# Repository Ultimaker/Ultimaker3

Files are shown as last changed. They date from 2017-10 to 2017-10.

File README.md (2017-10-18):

# Ultimaker 3
Ultimaker 3 Hardware Files

In this repository, you will find the documentation and hardware designs for all parts of the Ultimaker 3. The bill of materials (BOM) directory lists all parts, with part numbers, quantities and raw materials. Print core AA and print core BB have a separate BOM.

The electronics files can be found in the PCB files directory.
If you are missing a part or information feel free to file an issue on GitHub.

Harma Woldhuis <br>
Ultimaker

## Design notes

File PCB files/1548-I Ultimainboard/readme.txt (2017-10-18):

The UltiMainboard 2.x.x electronics are released under GPLv2 license.
And are based on the original Ultimaker electronics design by Jan-Jaap Schuurman, Siert Wijnia and ErikDeBruijn at http://reprap.org/wiki/Ultimaker's_v1.5.7_PCB
As well as the ArduinoMega2560 by Arduino: http://arduino.cc/en/Main/arduinoBoardMega2560

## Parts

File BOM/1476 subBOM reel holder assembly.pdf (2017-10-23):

1476 Reel holder assembly

Total quantity parts | | 7
Part number | | Name | Quantity | material
1724 | F | NFC spool holder | 1 | PC-ABS
1725 | G | NFC PCB cover | 1 | PC-ABS
1726 | B | NFC PCB Antenna | 1 | Multiple
1727 | C | NFC PCB Cable | 1 | Multiple
1728 | C | NFC PCB Cable Cover | 1 | 1.4301 (X5CrNi18-10)
1729 | H | Filament Guide Frame | 1 | PC-ABS
1734 | F | Filament Guide | 1 | POM Acetal Copolymer

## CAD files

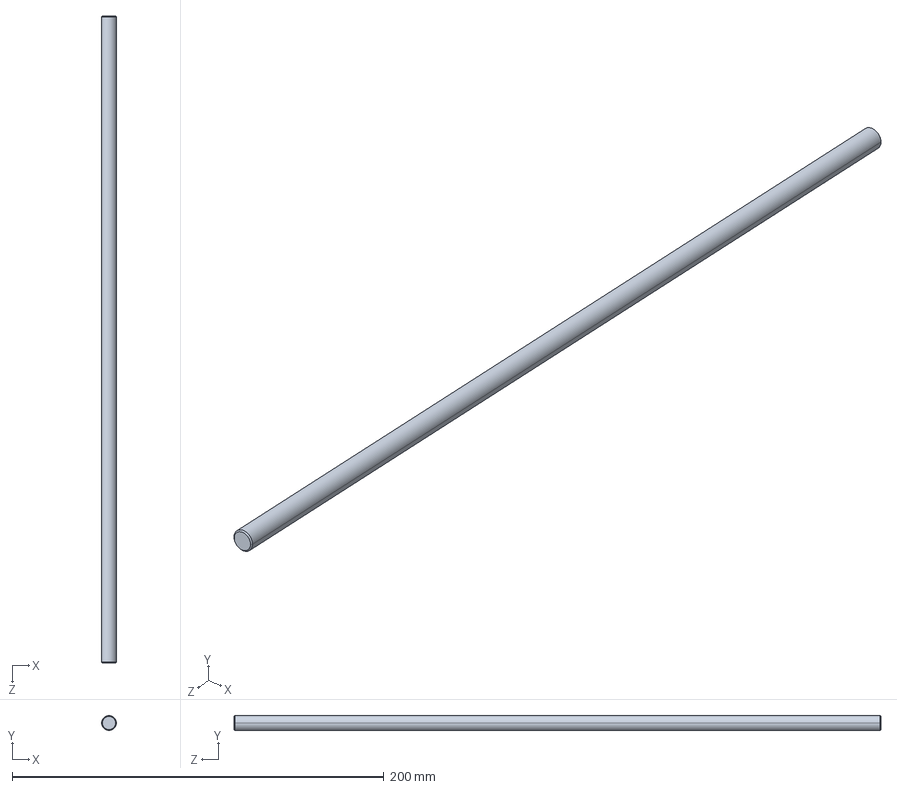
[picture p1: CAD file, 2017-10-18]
1011/1011-E/1011-E.STEP
8.00 x 8.00 x 348.0 mm

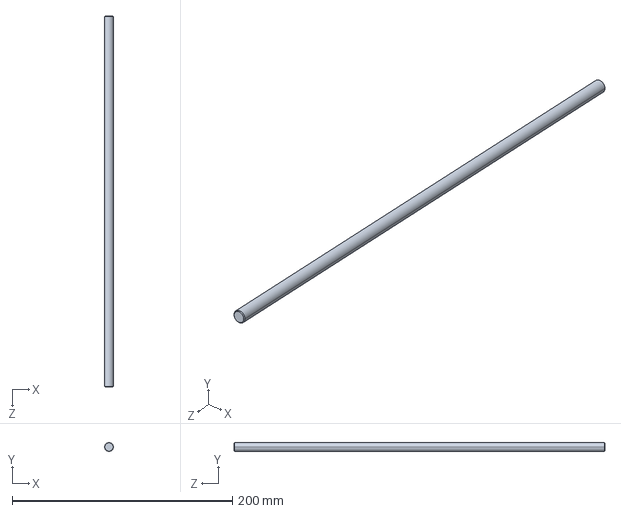
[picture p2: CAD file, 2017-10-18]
1012/1012-E/1012-E.STEP
8.00 x 8.00 x 337.0 mm

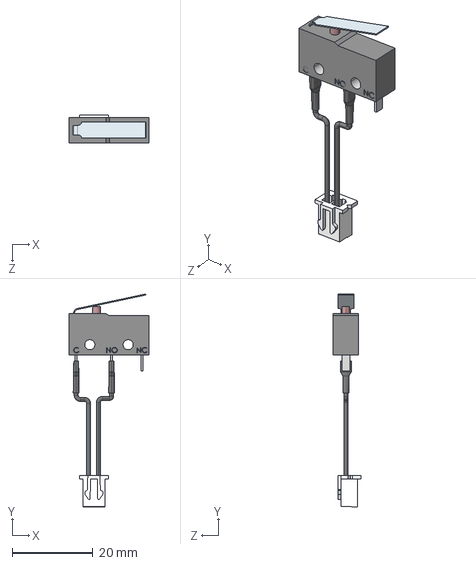
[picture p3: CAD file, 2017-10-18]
1024/1024-F/1024-F.STEP
19.8 x 52.9 x 6.90 mm

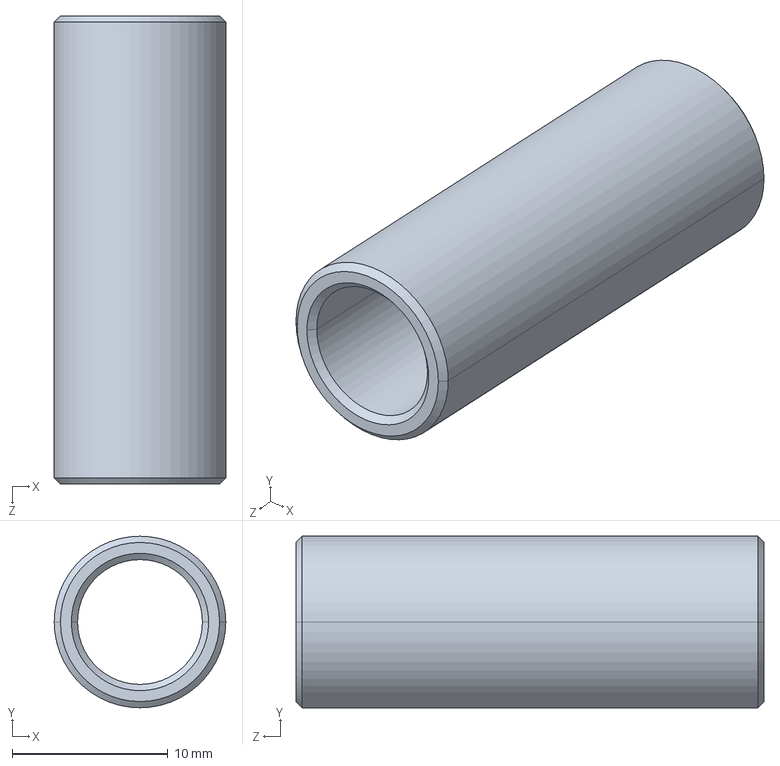
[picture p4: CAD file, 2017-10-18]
1056/1056-B/1056-B.STEP
11.0 x 11.0 x 30.0 mm

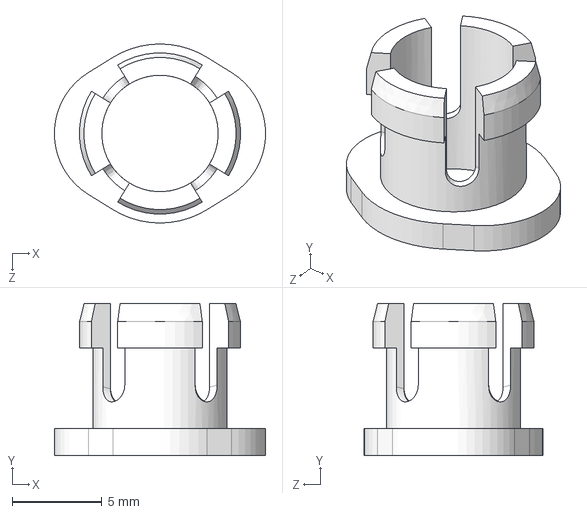
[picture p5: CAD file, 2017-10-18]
1069/1069-C/1069-C.STEP
11.8 x 8.50 x 10.00 mm

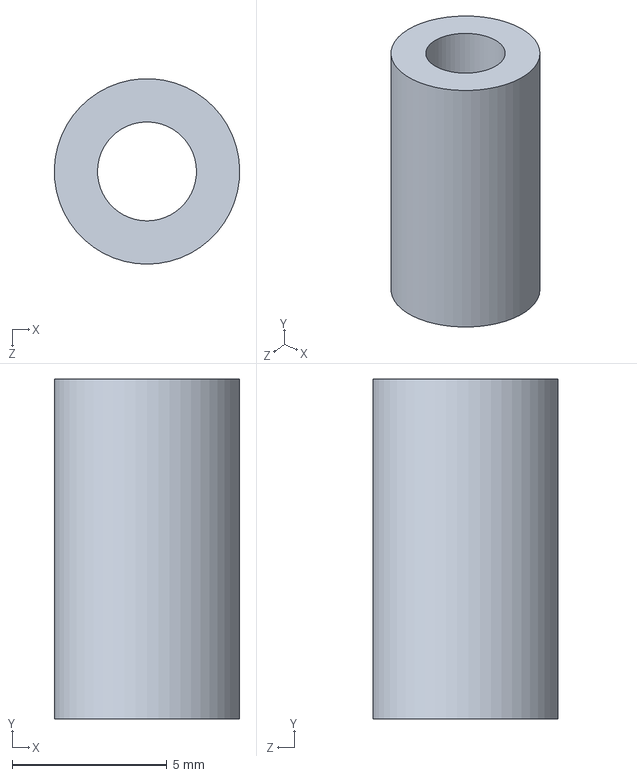
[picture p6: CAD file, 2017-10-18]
1083/1083-A/1083-Z1P-A.STEP
6.00 x 11.0 x 5.99 mm

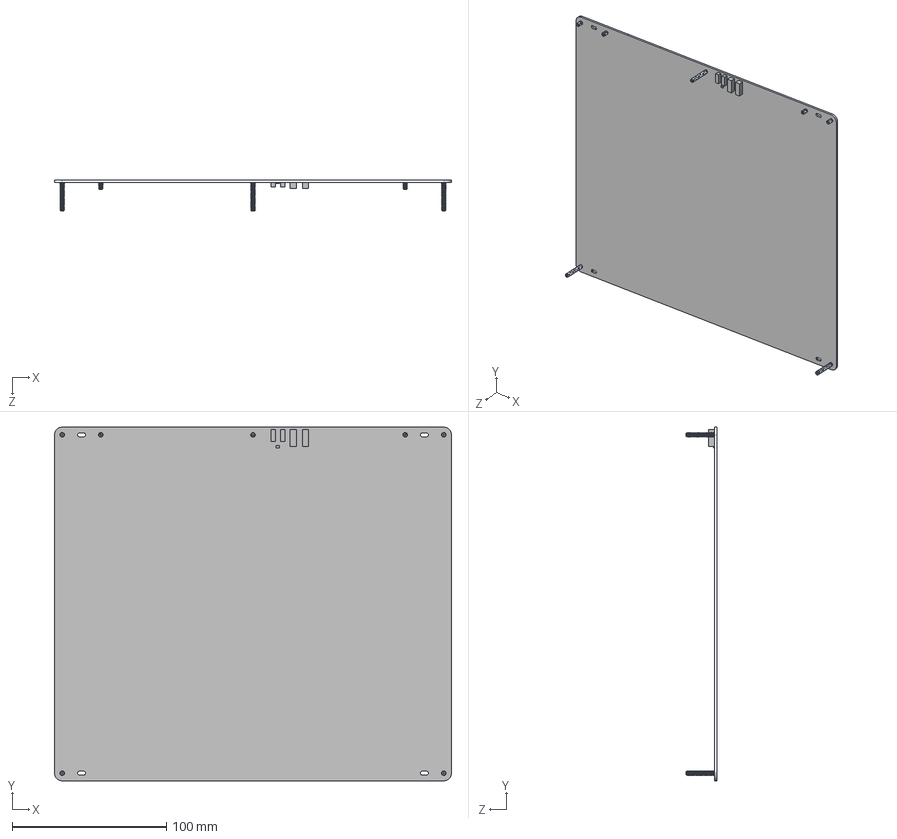
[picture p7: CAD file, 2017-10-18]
1155/1155-G/1155-G.STEP
257.0 x 229.0 x 20.0 mm
1155-D
FH-M3-xZI_FH-M3-6ZI x 4
FH-M3-xZI_FH-M3-20ZI x 3

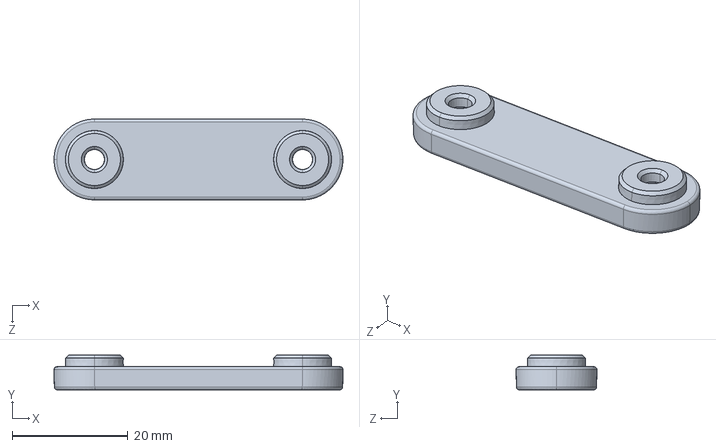
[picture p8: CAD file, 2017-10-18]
1156/1156-B/1156-B.STEP
50.0 x 6.00 x 14.0 mm

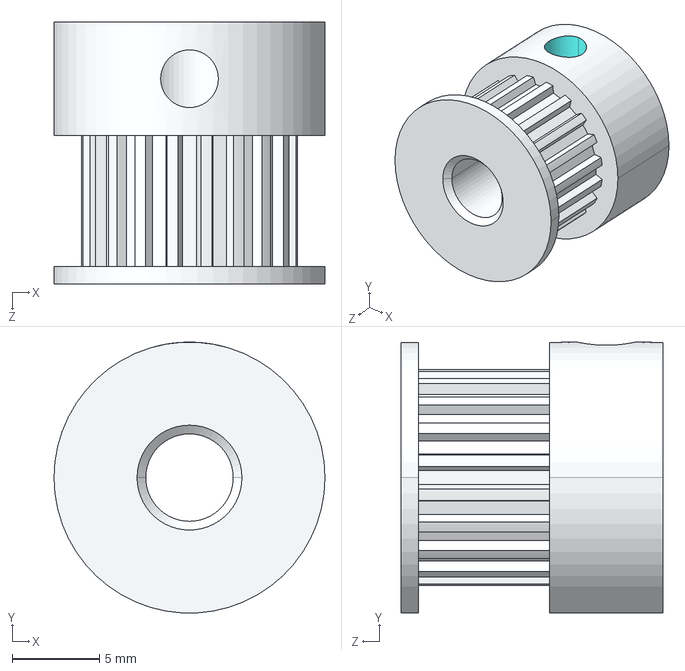
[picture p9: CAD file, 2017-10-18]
1165/1165-B/1165-B.STEP
15.5 x 15.5 x 15.0 mm

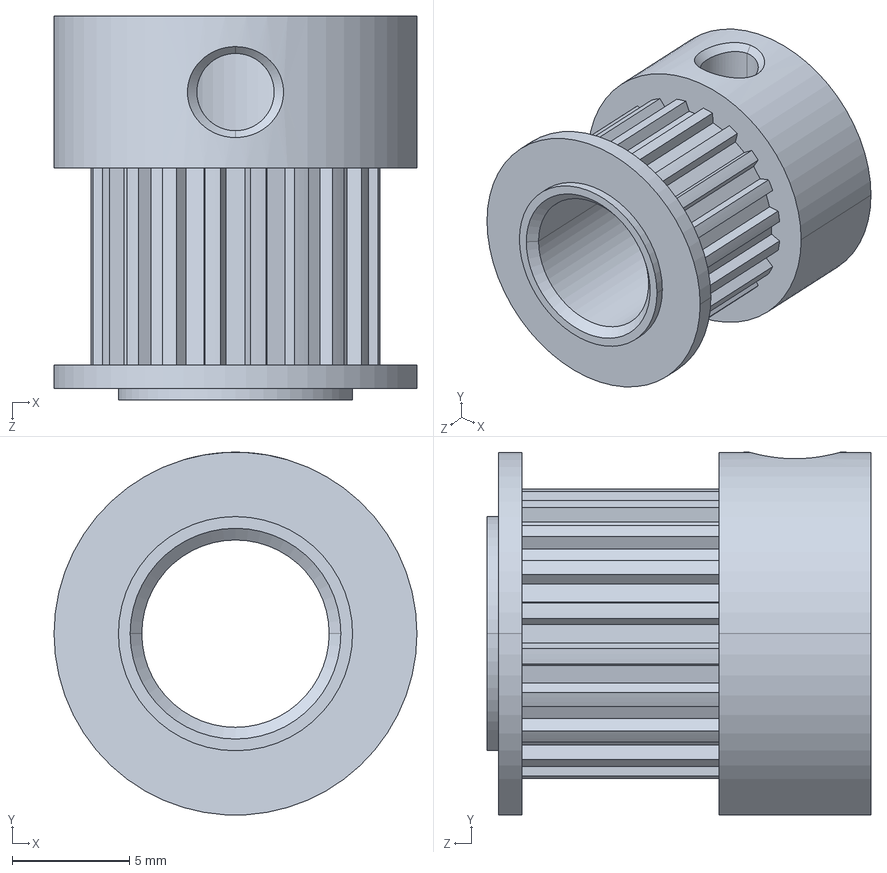
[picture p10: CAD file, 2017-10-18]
1166/1166-C/1166-C.STEP
15.5 x 15.5 x 16.4 mm

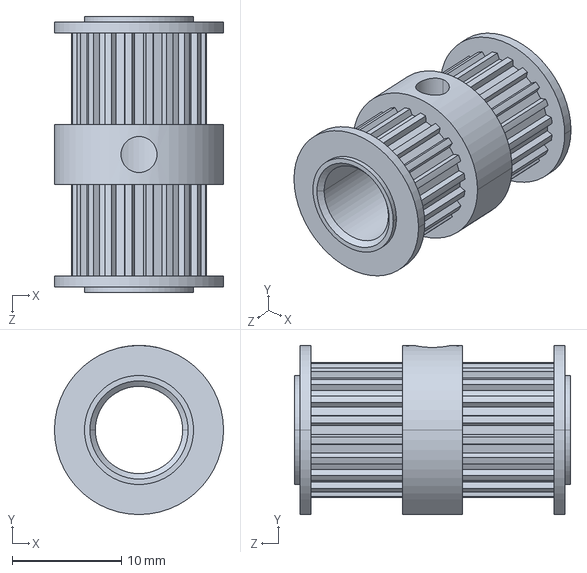
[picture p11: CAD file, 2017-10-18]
1167/1167-E/1167-E.STEP
15.5 x 15.5 x 25.3 mm

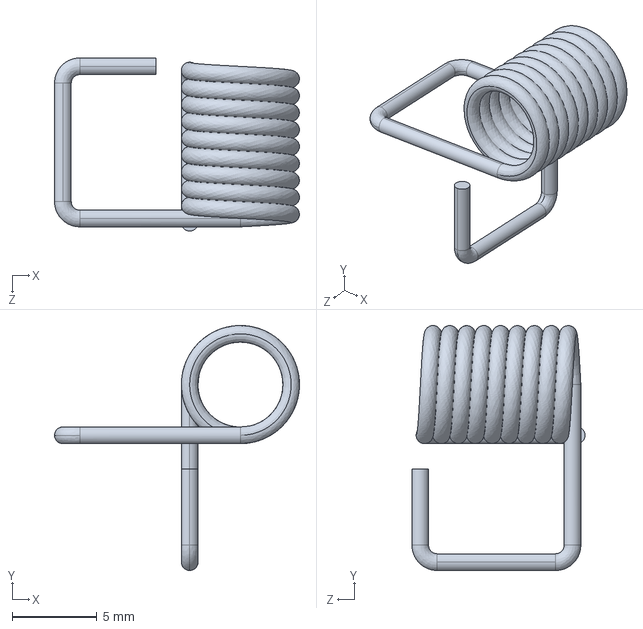
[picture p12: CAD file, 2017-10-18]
1168/1168-C/1168-C.STEP
14.5 x 14.5 x 10.2 mm

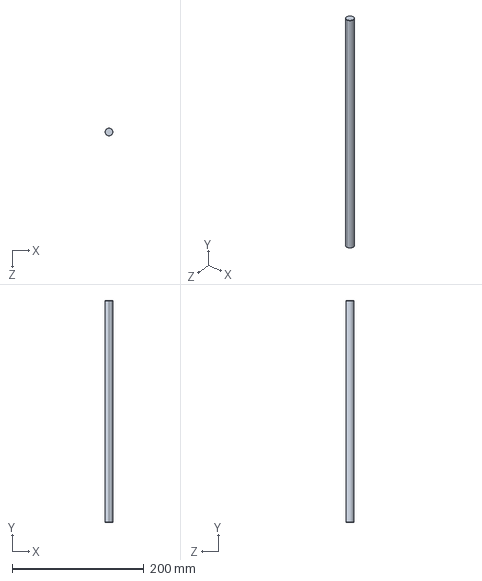
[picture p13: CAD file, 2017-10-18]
1169/1169-F/1169-F.STEP
12.0 x 337.0 x 12.0 mm

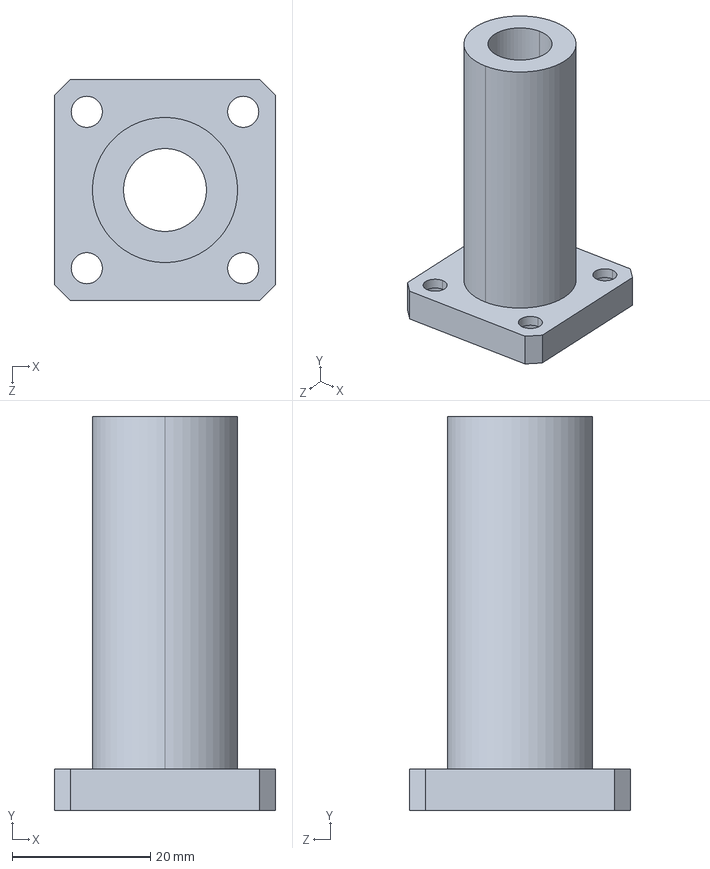
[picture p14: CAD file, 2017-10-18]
1170/1170-C/1170-C.STEP
32.0 x 57.0 x 32.0 mm

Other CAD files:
1172/1172-B/1172-B.STEP
1174/1174-A/1174-A.STEP
1175/1175-A/1175-A.STEP
1178/1178-B/1178-B.STEP
1187/1187-B/1187-B.STEP
1188/1188-A/1188-B2P-A.STEP
1200/1200-B/1200-B.STEP
1201/1201-D/1201-D.STEP
1202/1202-C/1202-C.STEP
1203/1203-C/1203-C.STEP
1204/1204-C/1204-C.STEP
1205/1205-C/1205-C.STEP
1206/1206-C/1206-C.STEP
1207/1207-C/1207-C.STEP
1209/1209-D/1209-D.STEP
1213/1213-C/1213-C.STEP
1214/1214-B/1214-B.STEP
1217/1217-B/1217-B.STEP
1220/1220-B/1220-B.STEP
1241/1241-C/1241-C.STEP
1244/1244-B/1244-B.STEP
1245/1245-D/1245-D.STEP
1252/1252-D/1252-D.STEP
1255/1255-B/1255-B.STEP
1256/1256-B/1256-B.STEP
1266/1266-D/1266-D.STEP
1279/1279-D/1279-D.STEP
1287/1287-B/1287-B.STEP
1288/1288-B/1288-B.STEP
1292/1292-A/1292-A.STEP
1294/1294-B/1294-B.STEP
1315/1315-B/1315-B.STEP
1354/1354-B/1354-B.STEP
1363/1363-D/1363-D.STEP
1479/1479-B/1479-B.STEP
1480/1480-B/1480-B.STEP
1481/1481-B/1481-B.STEP
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

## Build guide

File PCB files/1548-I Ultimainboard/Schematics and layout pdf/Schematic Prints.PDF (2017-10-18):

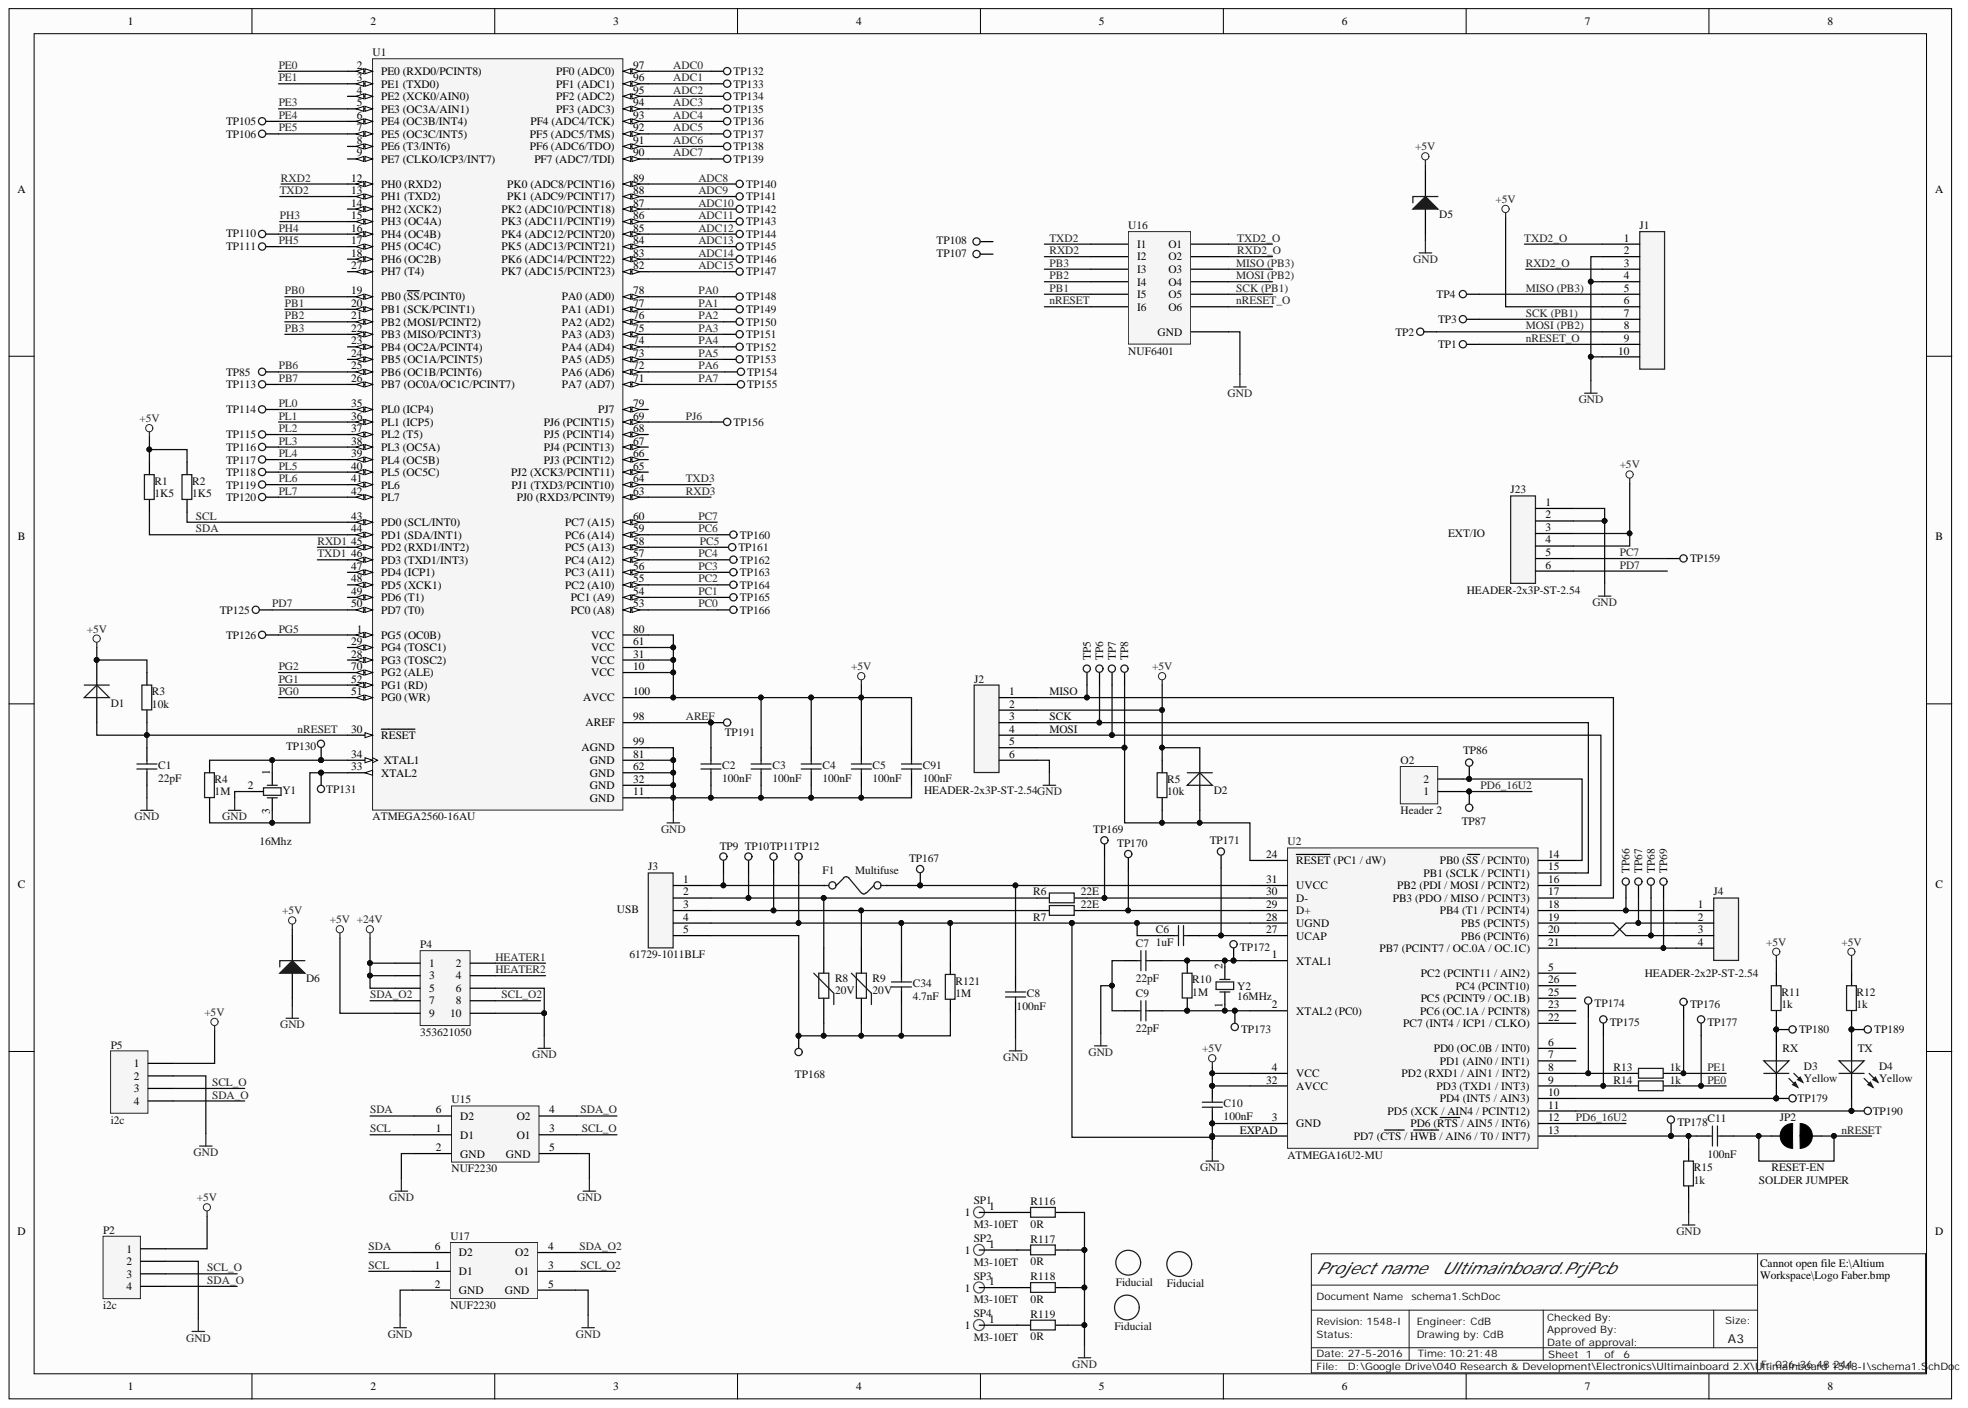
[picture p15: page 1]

3 | SCK
4 | MOSI

Project name Ultimainboard.PrjPcb

Cannot open file E:\Altium
Workspace\Logo Faber.bmp

Revision: 1548-I Status: | Engineer: CdB Drawing by: | Checked By: Approved By: Date of approval: | Size: A3

Date: 27-5-2016 | Time: 10:21:48 | Sheet of 6

D:\Google Drive\040 Research & Development\Electronics\Ultimainboard 2.X\Ultimainboard 1548-I\schema1.SchDoc

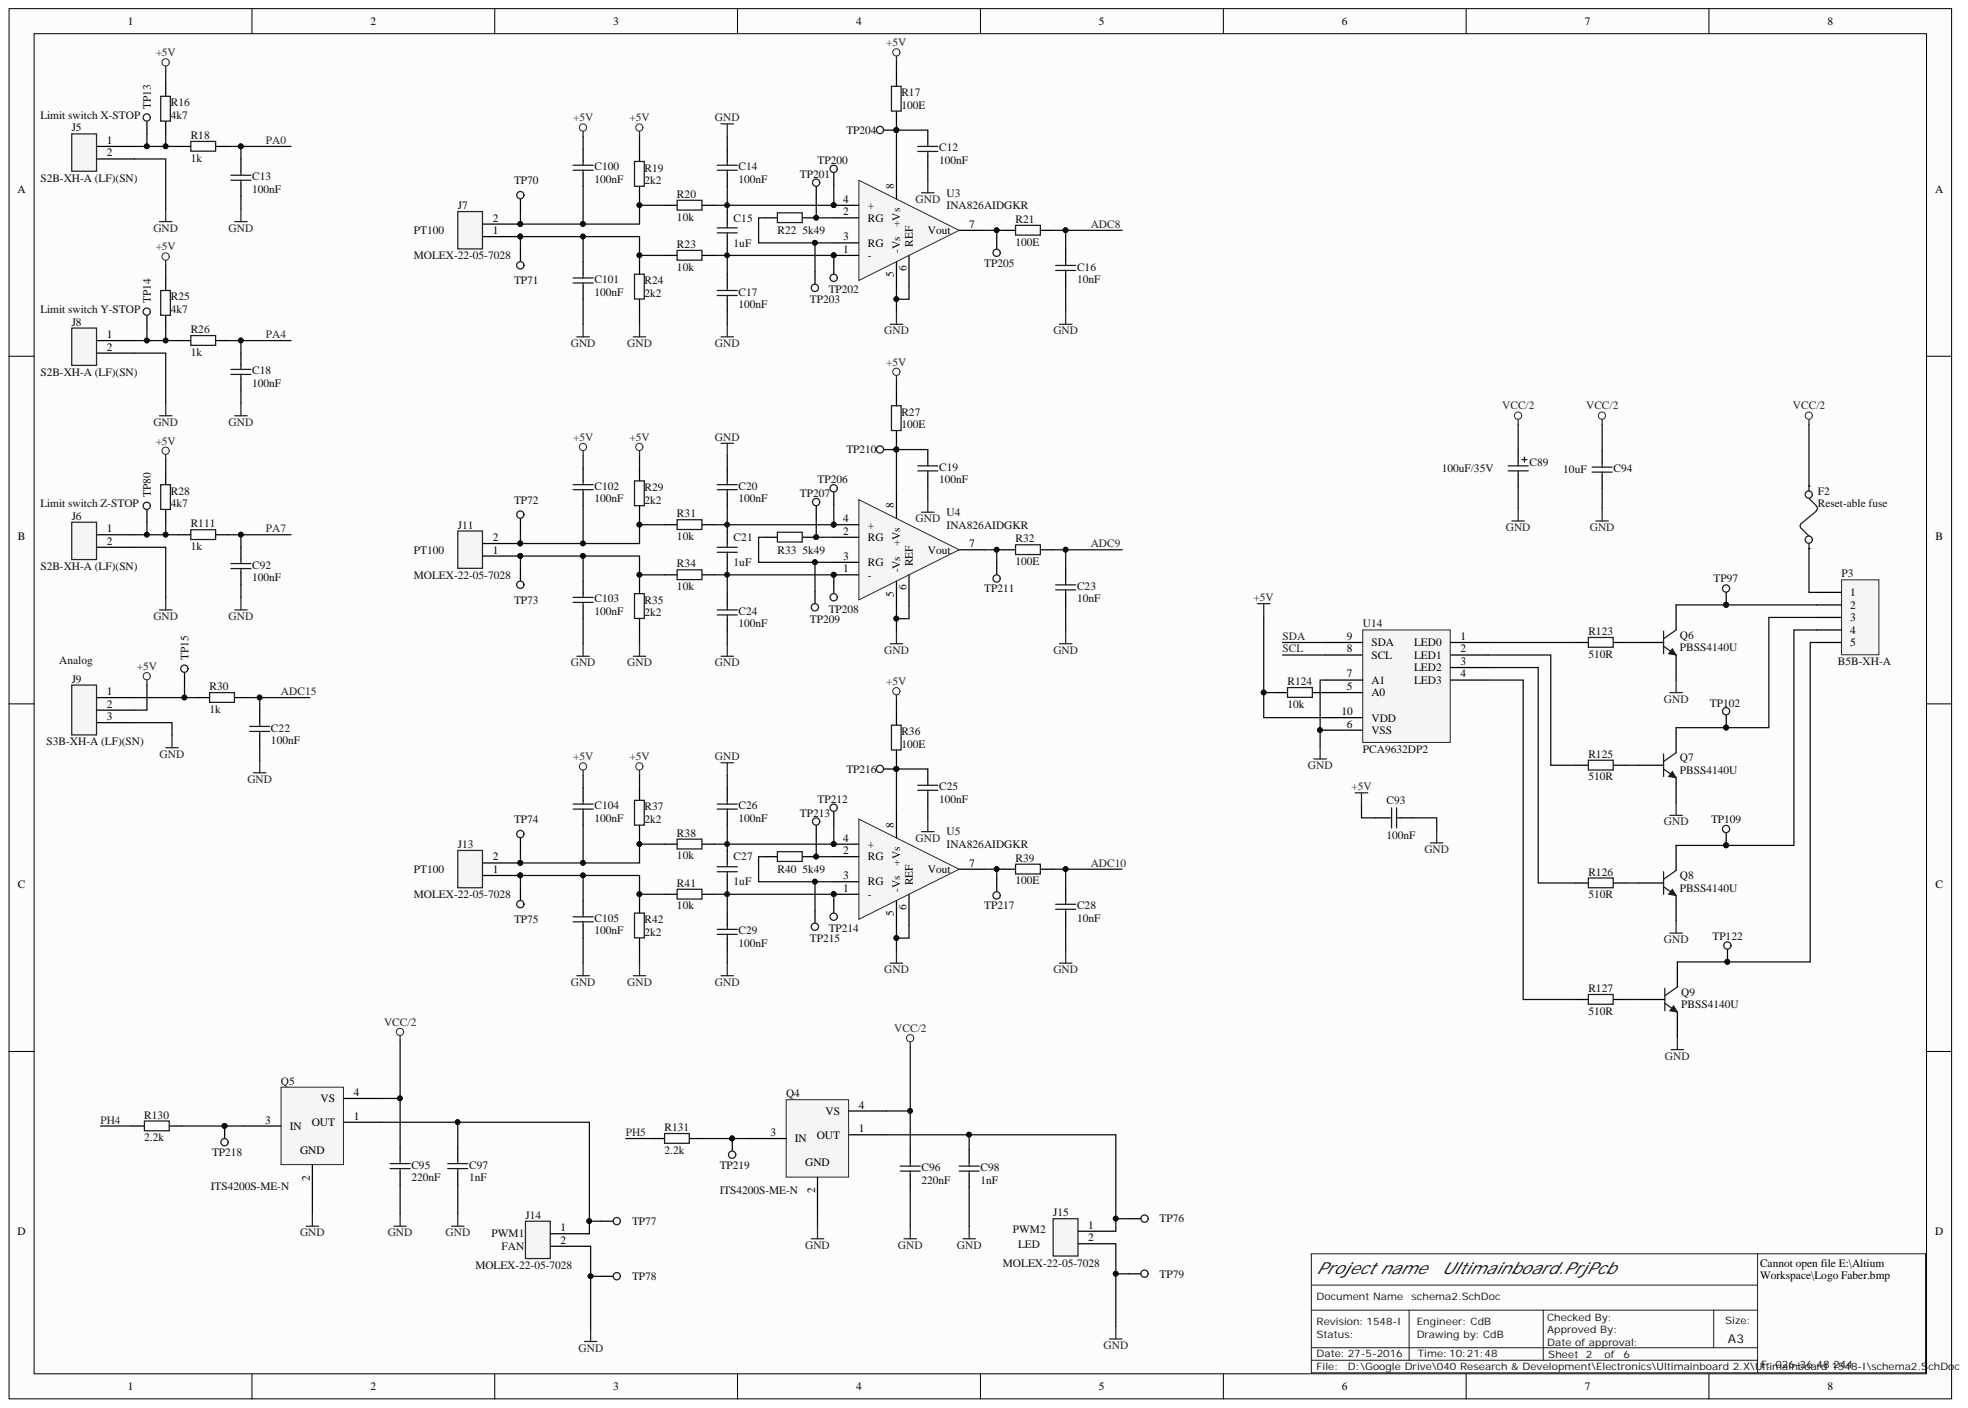
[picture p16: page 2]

Limit switch X-STOP Limit switch Y-STOP

Project name Ultimainboard.PrjPcb

Cannot open file E:\Altium
Workspace\Logo Faber.bmp

Engine e r : Cd B Dr a wing by: Cd B | Checke d By: A p p rove d By: Date of a p p roval: | Size : A

Date : 27-5-2016 | Time : 10:21:48 | She e t of

rch & Development\Electronics\Ultimainboa

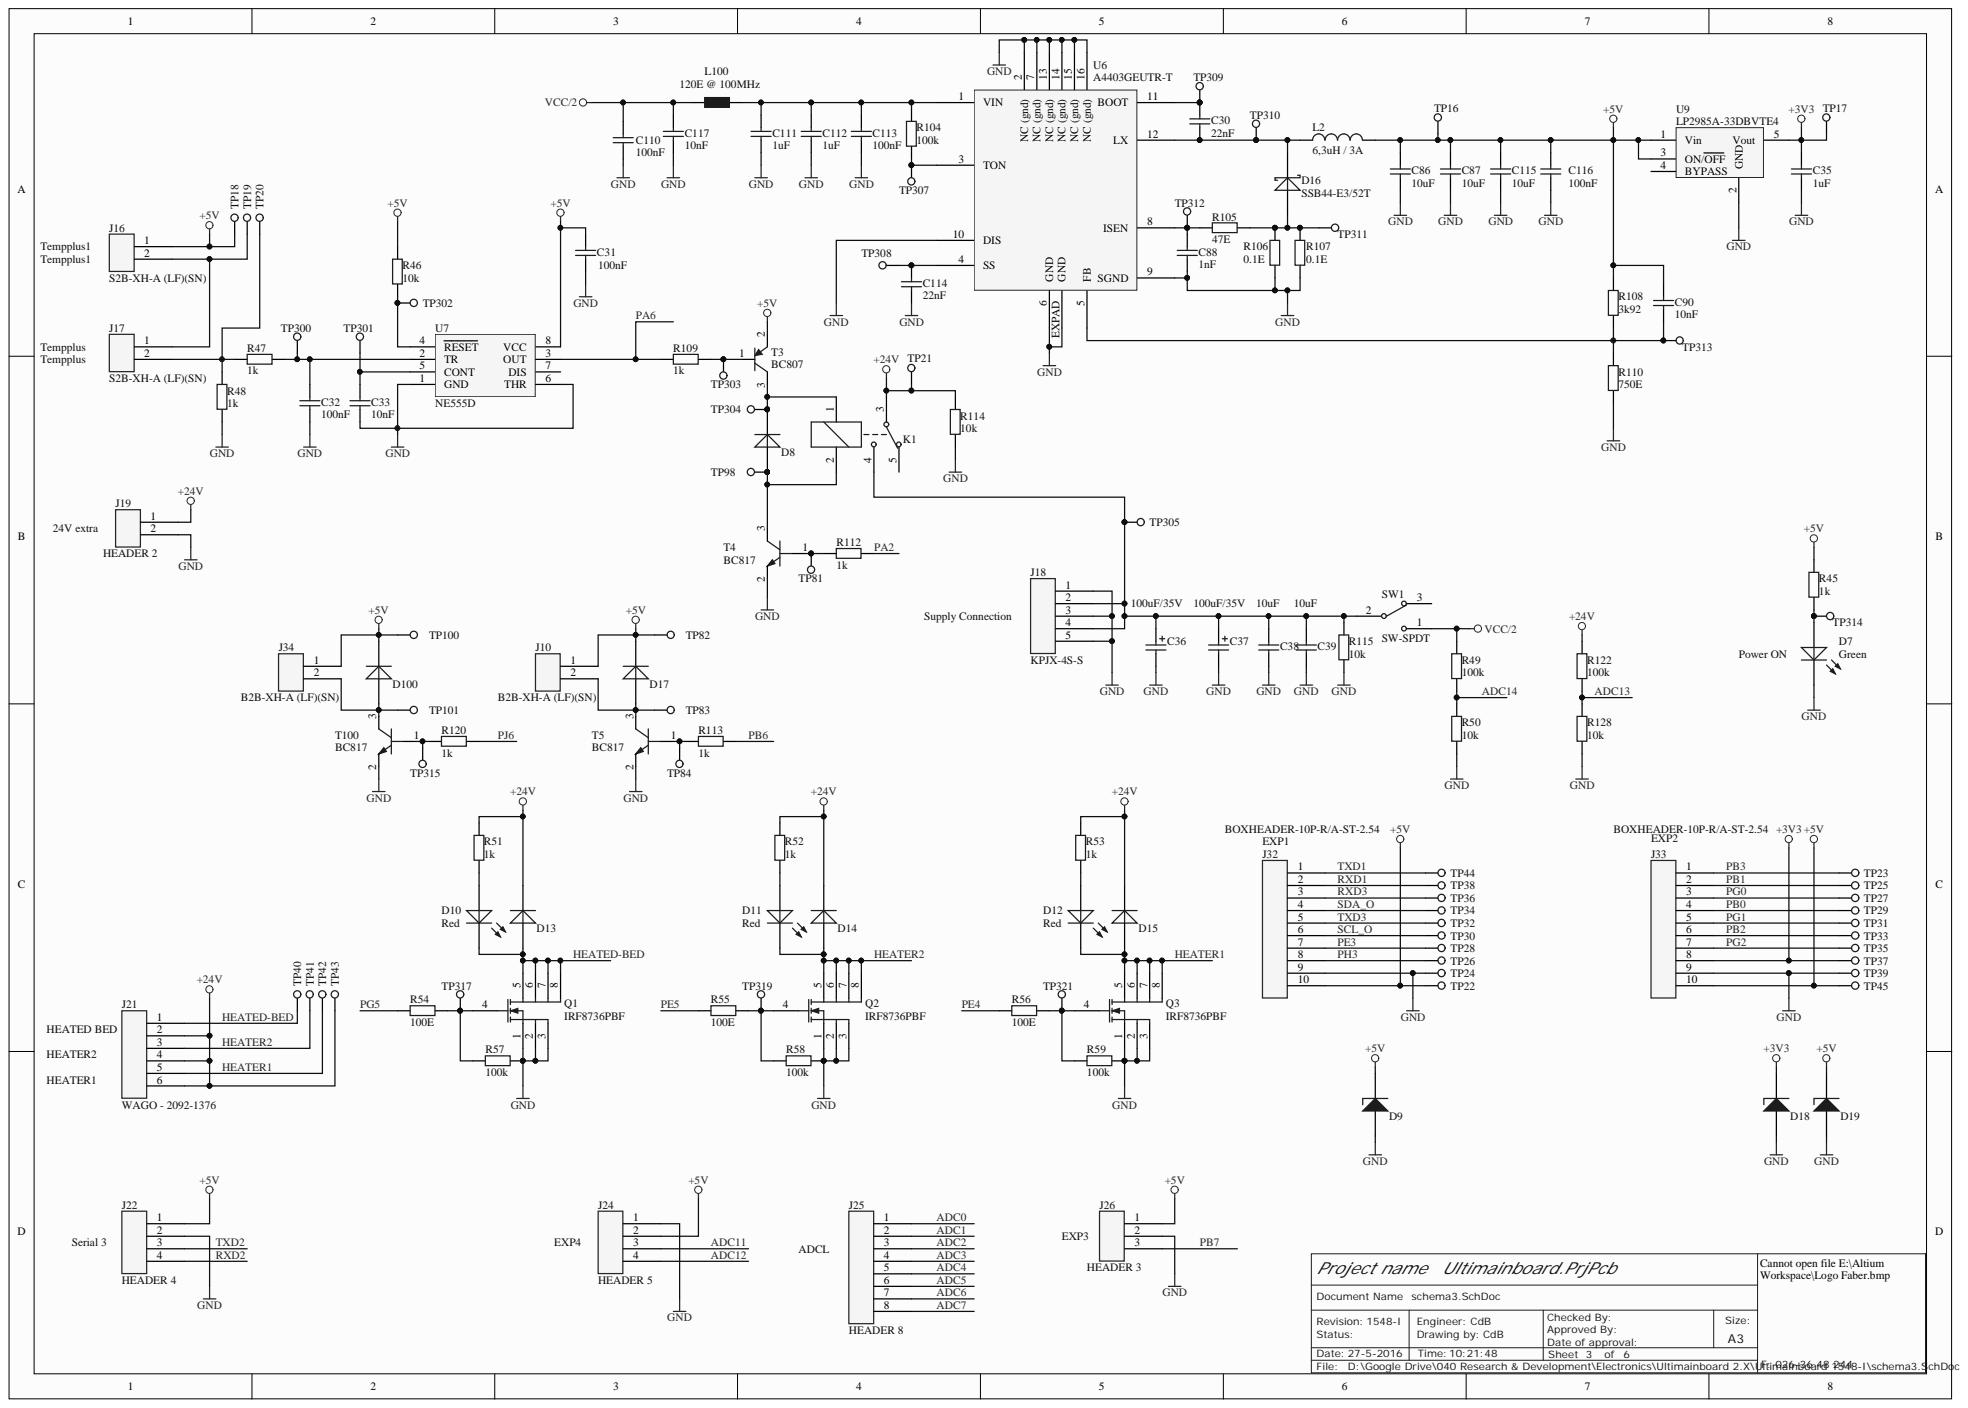
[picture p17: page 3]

TON 3

2 | HEATER2
4 | HEATER1

Project name Ultimainboard.PrjPcb

Cannot open file E:\Altium
Workspace\Logo Faber.bmp

D:\Google Drive\040 Research & Development\Electronics\Ultimainboard 2.X\Ultimainboard 1548-I\schema3.SchDoc

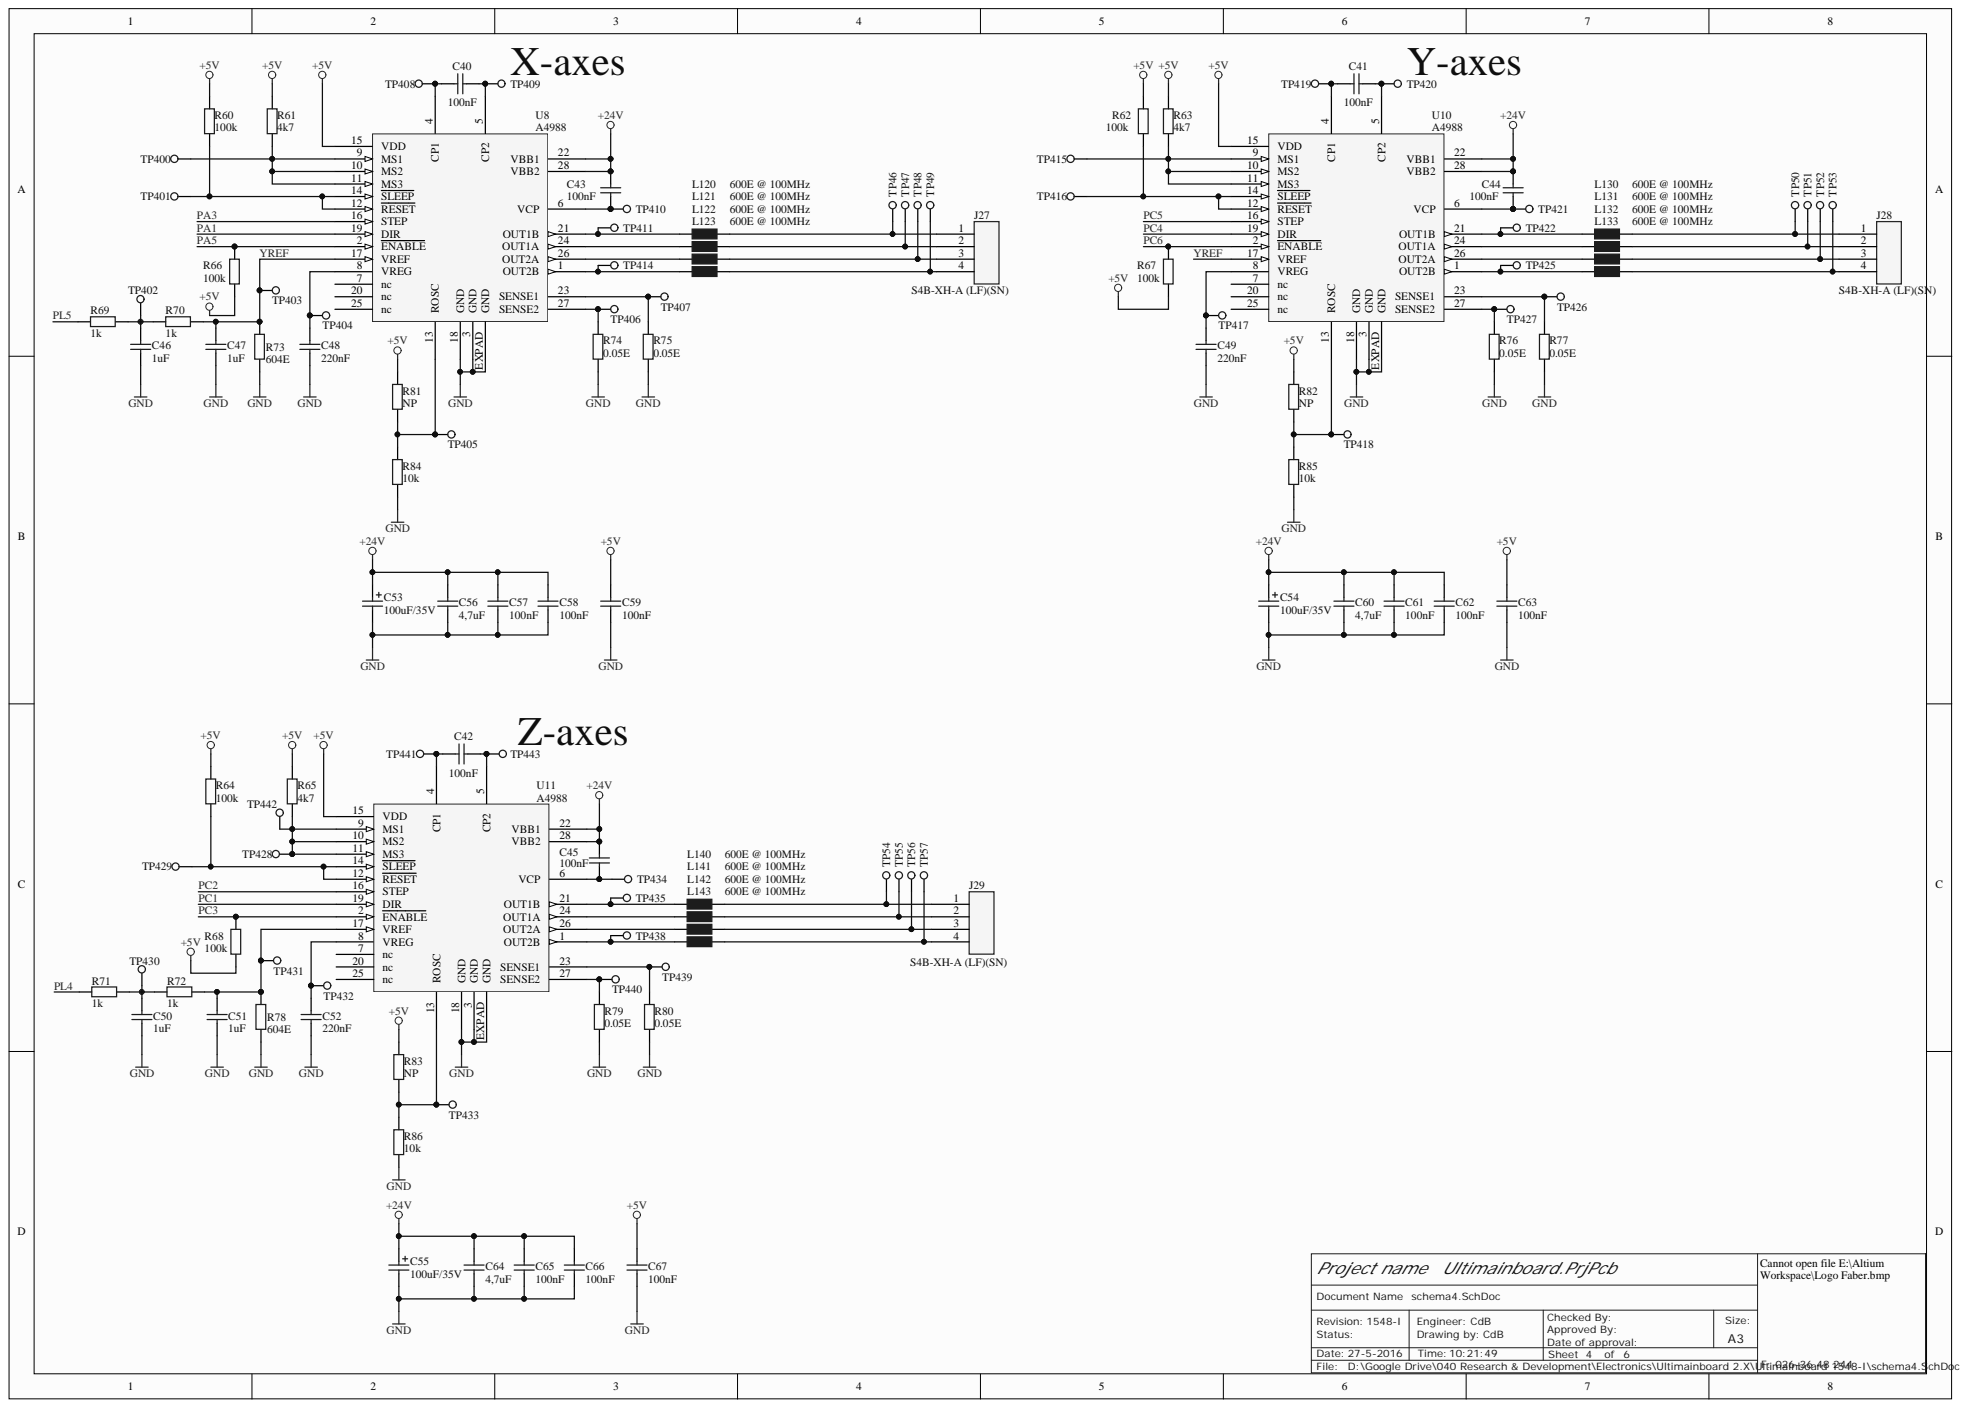
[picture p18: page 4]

VREG 8 | TP438 | 4
nc 7

Project name Ultimainboard.PrjPcb

Cannot open file E:\Altium
Workspace\Logo Faber.bmp

D:\Google Drive\040 Research & Development\Electronics\Ultimainboard 2.X\Ultimainboard 1548-I\schema4.SchDoc

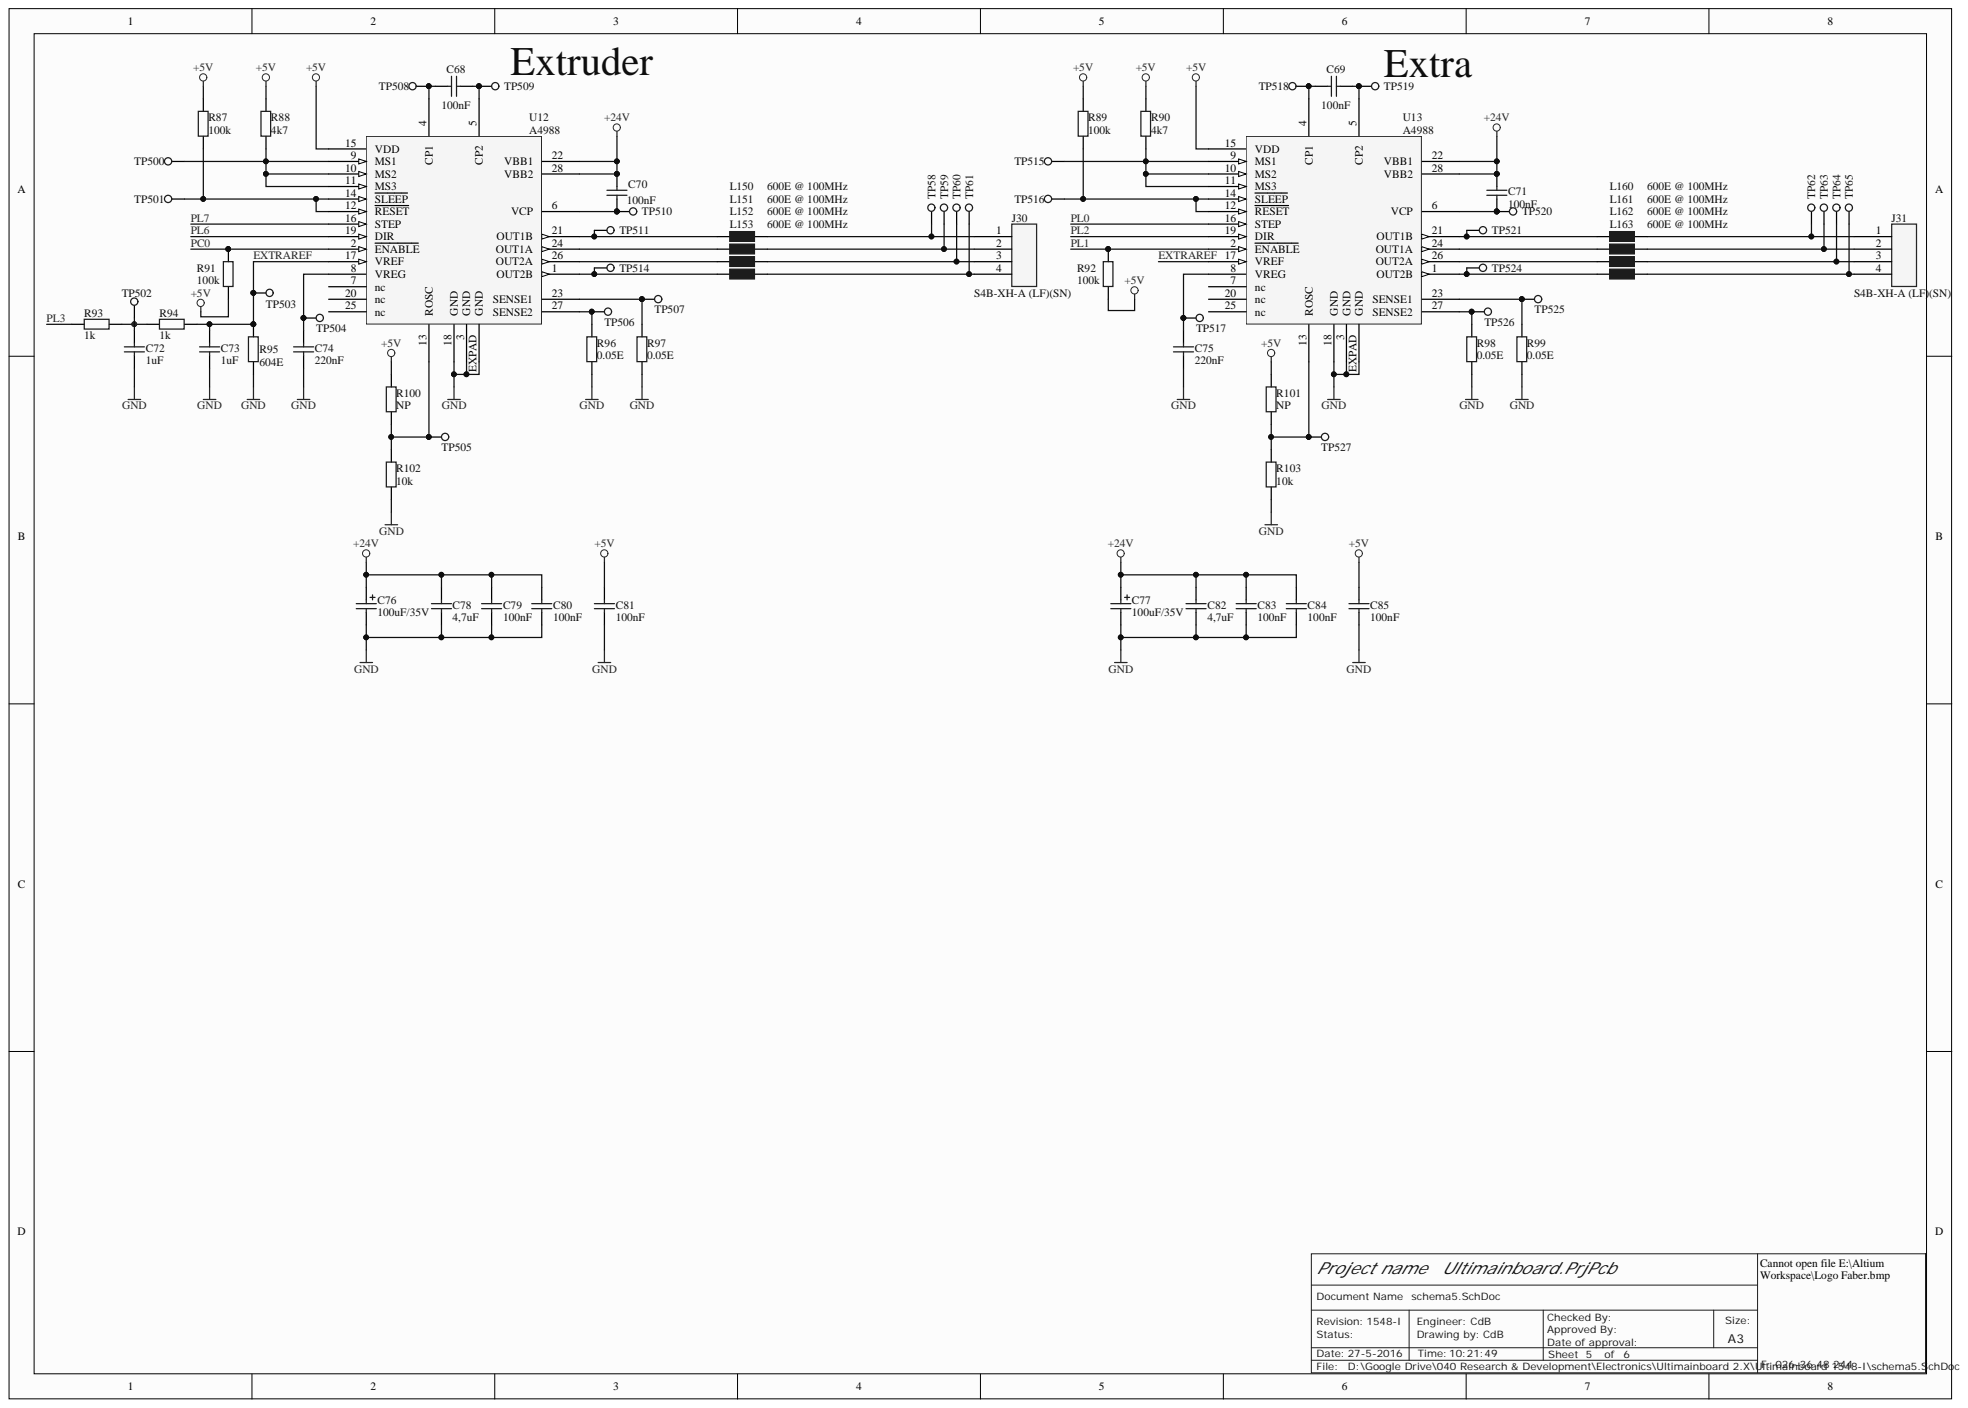
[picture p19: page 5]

Project name Ultimainboard.PrjPcb

Cannot open file E:\Altium
Workspace\Logo Faber.bmp

D:\Google Drive\040 Research & Development\Electronics\Ultimainboard 2.X\Ultimainboard 1548-I\schema5.SchDoc

D | D
C | C
B | B
A | A

D:\Google Drive\040 Research & Development\Electronics\Ultimainboard 2.X\Ultimainboard 1548-I\revisies.SchDoc

## Project name Ultimainboard.PrjPcb

revisies.SchDoc

Cannot open file E:\Altium Workspace\Logo Faber.bmp

## Revisies:

## Changes in respect to 1548-H CdB 26-05-2016 - Added D5, D6, D9, D18 and D19

## rev. 2.5 1548-H Changes in respect to rev. 2.4 1548-G CdB 21-03-2016 - Removed R43, R44, R129 and P1 CdB 21-03-2016 - Added U15, U16, U17 for ESD protection CdB 05-04-2016 - Changed U16 to NUF6401 CdB 06-04-2016 - Coupled TP107 and TP108 loose to remove antenna

## rev 2.4 (1548-G) Wijzigingen t.o.v. rev 2.3.1 CdB 05-11-2015 - J1 gewijzigd met extra GND pinnen voor betere signaal integriteit CdB 05-11-2015 - 22 ohm serie weerstanden toegevoegd aan i2c bus tegen reflecties CdB 05-11-2015 - 22 ohm serie weerstand toegevoegd aan seriele TX naar Printhead pcb

CdB 05-11-2015 - circuits van Q4 en Q5 aangepast aan datasheet eisen (C-tjes en input weerstanden toegevoegd)

## CdB 27-11-2015 - Changed R44 and R129 to 0 ohm CdB 27-11-2015 - Changed R43 to 82 ohm CdB 27-11-2015 - Removed paste from fiducials

## rev 2.3.1 (1548-F) Wijzigingen t.o.v. rev 2.3

CdB 10-09-2015 - Q4 en Q5 gewijzigd naar Infineon ITS4200S-ME-N, weerstanden verwijderd, lay-out iets aangepast

## rev 2.3 Wijzigingen t.o.v. 2.2.2

CdB 09-09-2015 - Extra spanningsdelere aan ADC gehangen voor controle goede werking relays

CdB 09-09-2015 - Zekering F2 toegevoegd voor RGBW leds CdB 09-09-2015 - Fan transistor gewijzigd naar smartfet Q5 CdB 24-08-2015 - Hirose connector P4 gewijzigd naar Molex CdB 24-08-2015 - 24 Fan connector en diode verwijderd CdB 24-08-2015 - Led power aan VCC/2 gehangen zodat leds aan kunnen zonder relays

CdB 24-08-2015 - Extruder aanduidingen E1 en E2 gewijzigd naar LEFT en RIGHT respectievelijk

## CdB 24-08-2015 - L en R aanduidingen toegevoegd voor filament detection aansluitingen CdB 24-08-2015 - Condensatoren toegevoegd voor RGBW leds

## rev 2.2.2 Wijzigingen t.o.v. 2.2.1

CdB 15-04-2015 - Sense weerstand sporen naar stepper drivers dunner gemaakt ivm. te hoge motorstroom en oververhitting van stepper drivers

## rev 2.2.1 Wijzigingen t.o.v. 2.2

CdB 28-01-2015 - Verwijderd (voor solenoid aansturing): R116 t/m R119, Q4, Q5, D18, D19 en P2

CdB 28-01-2015 - P5 verplaatst CdB 28-01-2015 - Extra i2c (P2) aansluiting toegevoegd CdB 28-01-2015 - R114 en R115 toegevoegd om condensatoren te ontladen CdB 28-01-2015 - R1 en R2 verlaagd naar 2k2 CdB 28-01-2015 - R116 - 119 toegevoegd om SP1 - 4 aan GND te hangen CdB 28-01-2015 - JP2 correct verbonden CdB 28-01-2015 - PT100 aanduidingen gewijzigd CdB 29-01-2015 - L1 verwijderd, C34 en R121 toegevoegd voor USB shield filter CdB 29-01-2015 - Straight JST connectoren silkscreen gewijzigd CdB 30-01-2015 - T2 vervangen door Q4 (smartfet), D6 verwijderd

rev. 2.2
Wijzigingen t.o.v. rev. 2.1.4:
CdB 10-10-2014 - P1, P4 en P5 toegevoegd voor i2c communicatie
CdB 10-10-2014 - O1 en O2 toegevoegd voor communicatie met Olimex board
CdB 10-10-2014 - R1 en R2 veranderd in 3K92
CdB 10-10-2014 - Toegevoegd voor solenoid aansturing: R116 t/m R119, Q4, Q5, D18, D19 en P2
CdB 10-10-2014 - Toegevoegd voor RGBW ledstrip aansturing: U14, R123 t/m R127, Q6 t/m Q9, P3, C93 CdB 10-10-2014 - R50 veranderd in 10K voor board identificatie
CdB 10-10-2014 - Toegevoegd voor schakelen relais: R112 en T4
CdB 10-10-2014 - Toegevoegd voor extra 5V fan aansluiting: J10, D17, T5, R113
CdB 10-10-2014 - J21 veranderd in Wago 2092-1376 met 12 gaten voor meer terminal mogelijkheden
CdB 10-10-2014 - JP3 verwijderd en doorverbonden, waardoor de Z stepper standaard op 1/16 step staat
CdB 10-10-2014 - TP400, 401, 415, 416, 428, 429, 442, 500, 501, 515 en 516 groter gemaakt voor full step modus en individueel uitschakelen steppers CdB 10-10-2014 - R66, R67, R68, R91 en R92 veranderd in 5V pull-up, zodat steppers standaard uit staan
CdB 10-10-2014 - Wijziging revisie tekst PCB in rev. 2.2, en ook aan onderkant toegevoegd
CdB 10-10-2014 - Twee gaten toegevoegd voor MDA testen
CdB 10-10-2014 - Board outline en formaat onder, rechts en boven opgeschoven zodat er minimaal 1,5mm zit tussen de rand en componenten CdB 10-10-2014 - Ultimaker tekst verwijderd van bovenkant
CdB 22-10-2014 - P4 toegevoegd voor pcb op printkop
CdB 24-10-2014 - Bottom solder van U2, U6, U8, U10, U11, U12 en U13 weg gehaald

rev. 2.1.4
Wijzigingen t.o.v. rev. 2.1.3:
RT (20-05-2014) - BOM wijziging, ferriets bij motorsturing gewijzigd in fabrikant nummer: 742792118 (Wurth Elektronic) RT (08-05-2014) - PCB verbreden (13mil) van de spoortjes van de sense weerstanden naar de stepper drivers

rev. 2.1.3
Wijzigingen t.o.v. rev. 2.1.2:
RT (06-03-2014) - Wijziging revisie tekst PCB in rev. 2.1.3
RT (06-03-2014) - Verwijderd C120 t/m C123, C130 t/m C133, C140 t/m C143, C150 t/m C153, C160 t/m C163
RT (06-03-2014) - Gewijzigd L120 t/m L123, L130 t/m L133, L140 t/m L143, L150 t/m L153, L160 t/m L163 in MLB-321611-0500PP

rev. 2.1.2
Wijzigingen t.o.v. rev. 2.1.1:
RT (03-01-2013) - Wijziging revisie tekst PCB in rev. 2.1.2
RT (03-01-2013) - Testpads toegevoegd voor MDA test
RT (03-01-2013) - Tekst "Ultimaker" PCB aangepast
RT (03-01-2013) - Logo verwijderd PCB
RT (18-12-2013) - Toegevoegd cap (Voeding 5V): C110, C111, C112, C113, C114, C115, C116, C117 RT (18-12-2013) - Toegevoegd Ferriet (Voeding 5V): L100
RT (18-12-2013) - Verwijderd (Voeding 5V): C34, C89
RT (18-12-2013) - Toegevoegd (Fan 5V): D100, T100, R120
RT (18-12-2013) - Toegevoegd (X-axes): L120, L121, L122, L124, C120, C121, C122, C123 RT (18-12-2013) - Toegevoegd (X-axes): L130, L131, L132, L134, C130, C131, C132, C133 RT (18-12-2013) - Toegevoegd (X-axes): L140, L141, L142, L144, C140, C141, C142, C143 RT (18-12-2013) - Schemablad toegevoegd (schema5)
RT (18-12-2013) - Toegevoegd (Extruder): L150, L151, L152, L154, C150, C151, C152, C153
RT (18-12-2013) - Toegevoegd (Extra): L160, L161, L162, L164, C160, C161, C162, C163
RT (18-12-2013) - Gewijzigd R106 en R107 in 0805
RT (18-12-2013) - Footprints aangepast van J1, J2, J3, J4, J23, J32 en J33 . Solder thiefs toegevoegd botttom side.

rev. V2.1.1
Wijzigingen t.o.v. rev. V2.1:
RT (27-06-2013) - C100 t/m C105 (100nF) toegevoegd
RT (28-06-2013) - J34 (B2B-XH-A (LF)(SN)) toegevoegd
RT (28-06-2013) - SP1 t/m SP4 (M3-10ET ) toegevoegd
RT (28-06-2013) - Layout: Ultiboard 2.1 wordt Ultimainboard 2.1.1 (silkscreen tekst)
RT (28-06-2013) - Layout: www.ultimaker.com/ub21 wordt www.ultimaker.com/umb211 (silkscreen tekst)

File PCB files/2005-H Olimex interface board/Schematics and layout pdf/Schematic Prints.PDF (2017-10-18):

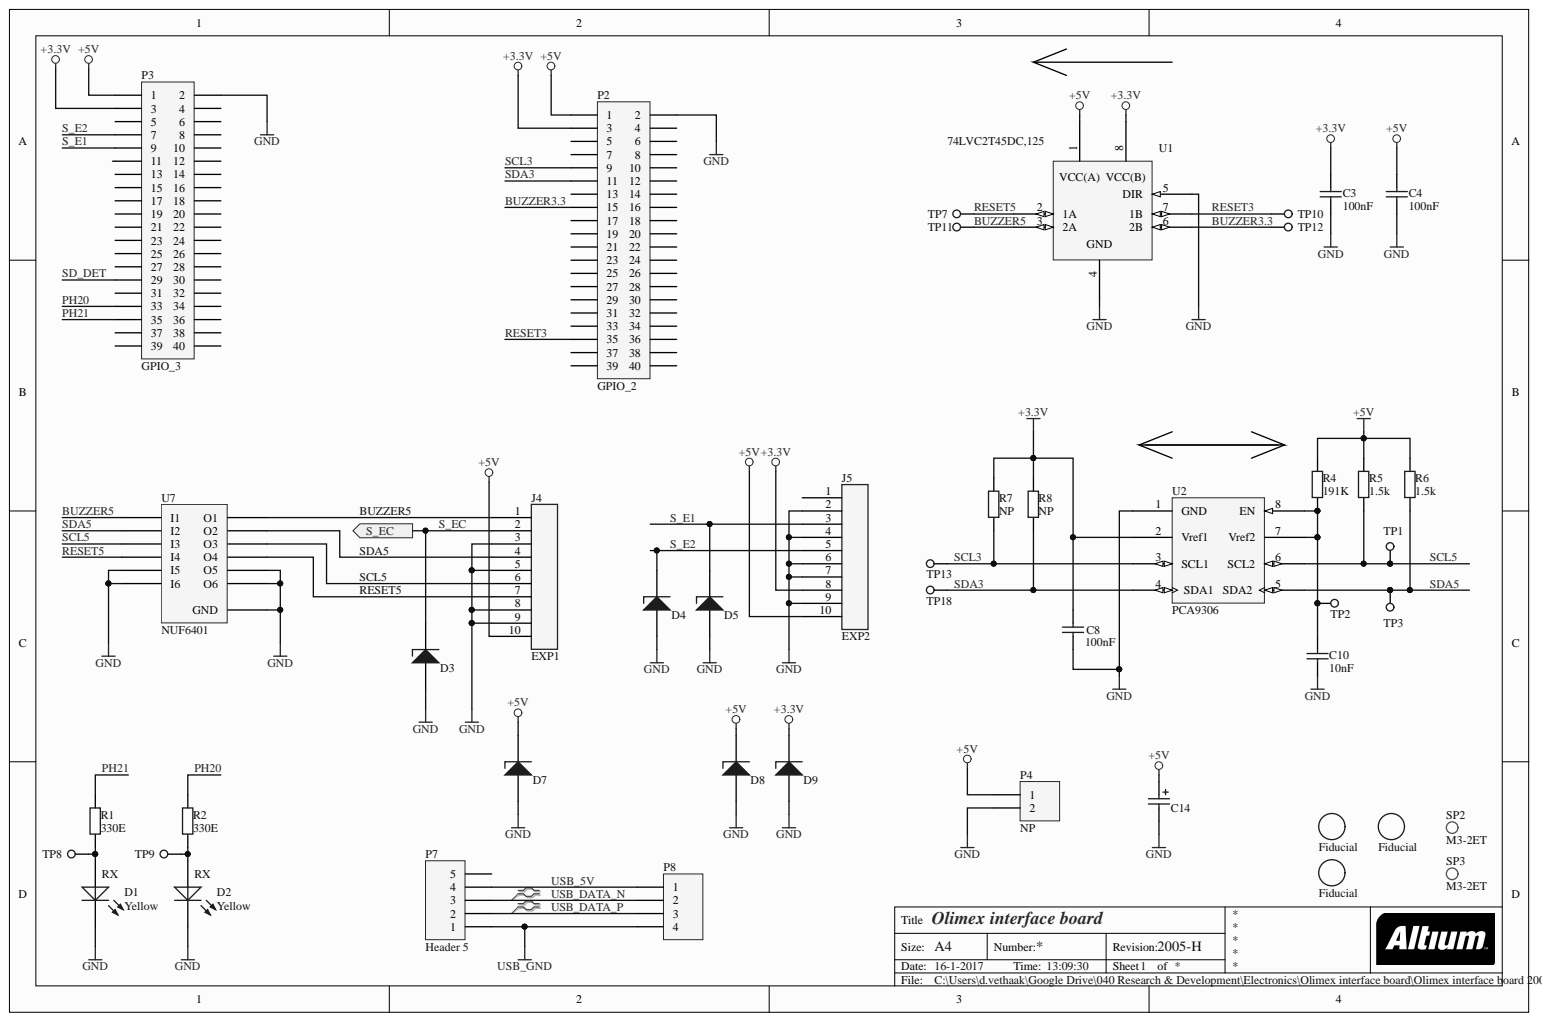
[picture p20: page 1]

SDA5 | | | 4

10

RESET5 | | | 7

Olimex interface board Title | * * * * *

Size: A4 | Number: * | Revision: 2005-H
Date: 16-1-2017 Time: 13:09:30 | | Sheet of *

C:\Users\d.vethaak\Google Drive\040 Research & Development\Electronics\Olimex interface board\Olimex interface board 2005-H\Schema1.SchDoc

D | D
C | C
B | B
A | A
Olimex Interface Board Title | * * * *
Size: A4 | Number: * | Revision: 2005-H
| | *
C:\Users\d.vethaak\Google Drive\040 Research & Development\Electronics\Olimex interface board\Olimex interface board 2005-H\Revisions.SchDoc

Revisions:

2005-H
DJV 16-01-2017 canged schematics and bom. PCB as 2005-G version. R11 R12 i2c pull ups are change from 1k5 to 4k7. R5 R6 are must stay 1.5K

2005-G
Changes in respect to 2005-F
CDB 27-05-2016 - Connected J1 mechanical pins to GND for stronger connection

CDB 26-05-2016 - Added C14, D7, D8, D9 and D10
CDB 26-05-2016 - Changed D3, D4 and D5 to ESD9X3.3ST5G
CDB 26-05-2016 - Changed D6 to ESD9X5.0ST5G

Rev 1.2 2005-F
Changes in respect to rev 1.1
CdB 11-04-2016 - Mirrored PCA9306 chips to follow datasheet
CdB 11-04-2016 - Changed U1 to 74LVC2T45DC,125
CdB 11-04-2016 - Removed R23, R24, R25, R6, R3, R10, R22, C7, C3, J6, J1 and J7 CdB 11-04-2016 - Added D3, D4, D5, U6, U7, U8, J1
CdB 11-04-2016 - Changed board shape

CdB 13-04-2016 - Connected via's directly to ground and power planes
CdB 13-04-2016 - Connected P1, P2, P3, P5 and P6 power pins directly to ground and power planes

rev 1.1 2005-E
Changes in respect to rev. 1.0
CdB 07-12-2015 - Removed fan circuit
CdB 07-12-2015 - Changed SP1 to NPTH
CdB 07-12-2015 - Added female header P7 for wifi board CdB 07-12-2015 - Added connector P8
CdB 07-12-2015 - Removed R14 and R15
CdB 14-12-2015 - Changed board shape

rev 1.0 2005-D
Changes in respect ro rev. 0.9
CdB 05-11-2015 - Added I2C connector and voltage translator for RFID CdB 05-11-2015 - Changed J3 routing for better signal intergrity
CdB 05-11-2015 - Added series resistor to TX output to prevent overshoot

CdB 27-11-2015 - Changed P5 from Not Populated to Populated
CdB 05-11-2015 - Changed R10 to 82 ohm
CdB 05-11-2015 - Changed SP1 to Not Populated
CdB 05-11-2015 - Changed R14 and R15 to 0 ohm

rev. 0.9
Changes in respect ro rev. 0.8
CdB 09-09-2015 - Switched around fan and buzzer pins

rev. 0.8
Changes in respect to rev. 0.7
CdB 15-05-2015 - Removed resistors R10 - R17
CdB 15-05-2015 - Re-routed tracks through P1, P2, P3, P5 and P6 connectors

rev. 0.7
Changes in respect to rev 0.6
CdB 20-04-2015 - Plated holes in P1, P2, P3, P5 and P6

rev. 0.6
Changes in respect to rev 0.5
CdB 20-04-2015 - Replaced LSF0108 voltage translators with translating transceivers CdB 20-04-2015 - Added PCA9306 for i2c communication
CdB 20-04-2015 - Switched 0ohm resistors from SD pins to SPI pins

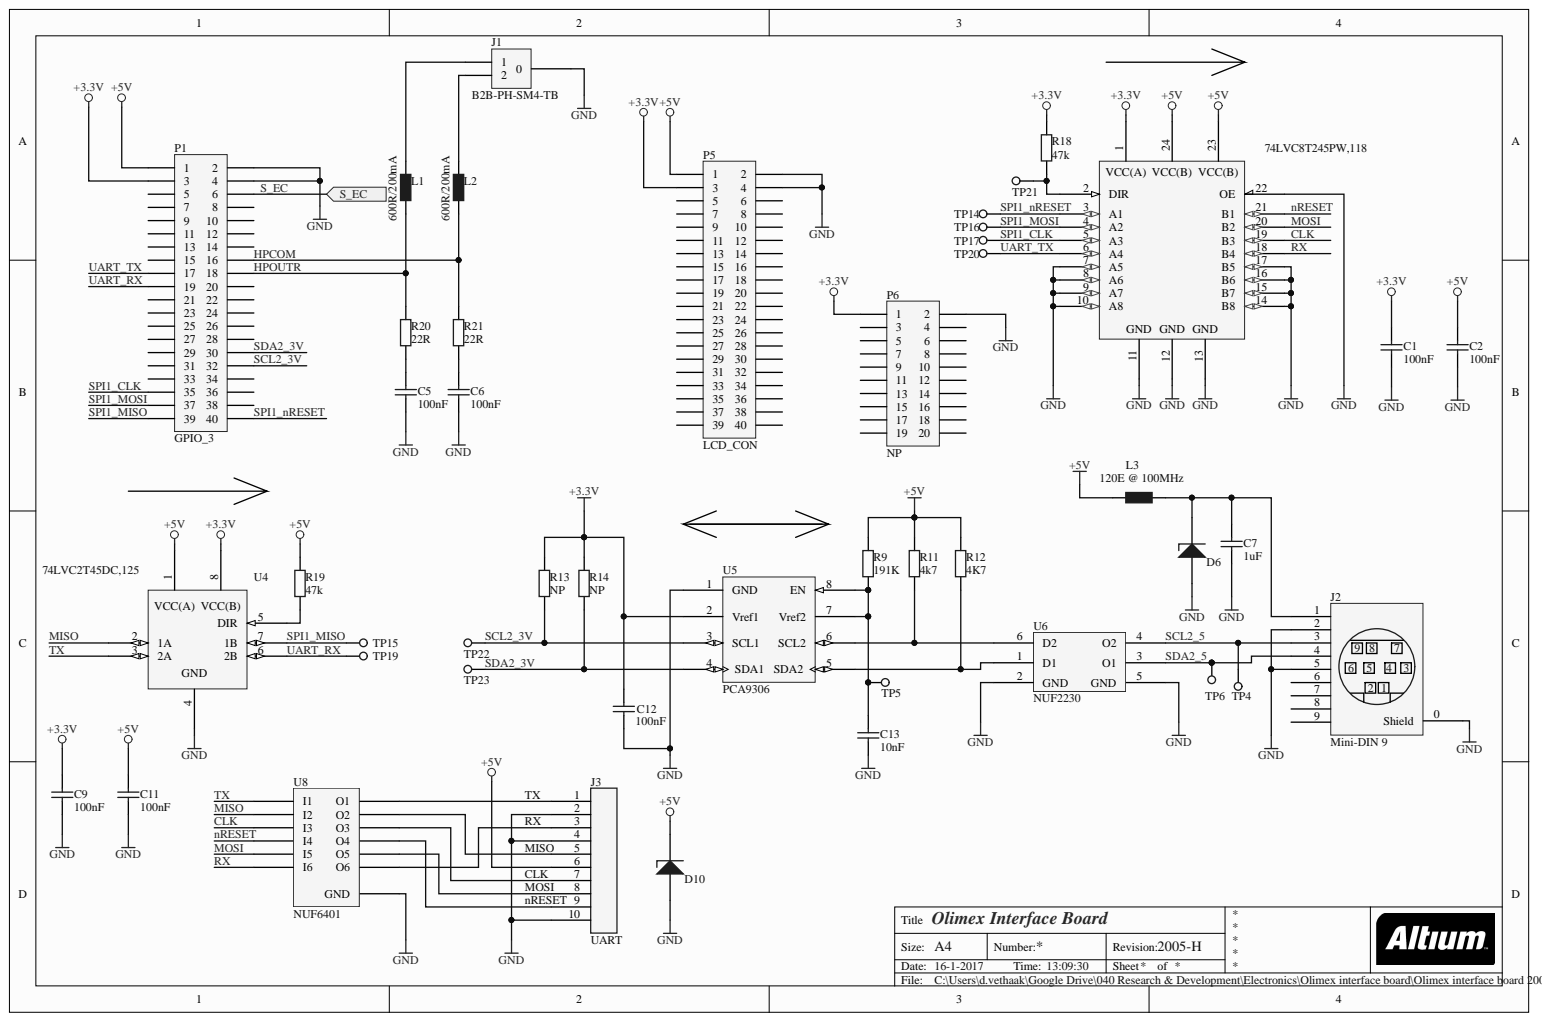
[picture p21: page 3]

MISO | 5

CLK | 7
MOSI | 8
nRESET | 9

Size: A4 | Number: * | Revision: 2005-H

C:\Users\d.vethaak\Google Drive\040 Research & Development\Electronics\Olimex interface board\Olimex interface board 2005-H\Schema2.SchDoc

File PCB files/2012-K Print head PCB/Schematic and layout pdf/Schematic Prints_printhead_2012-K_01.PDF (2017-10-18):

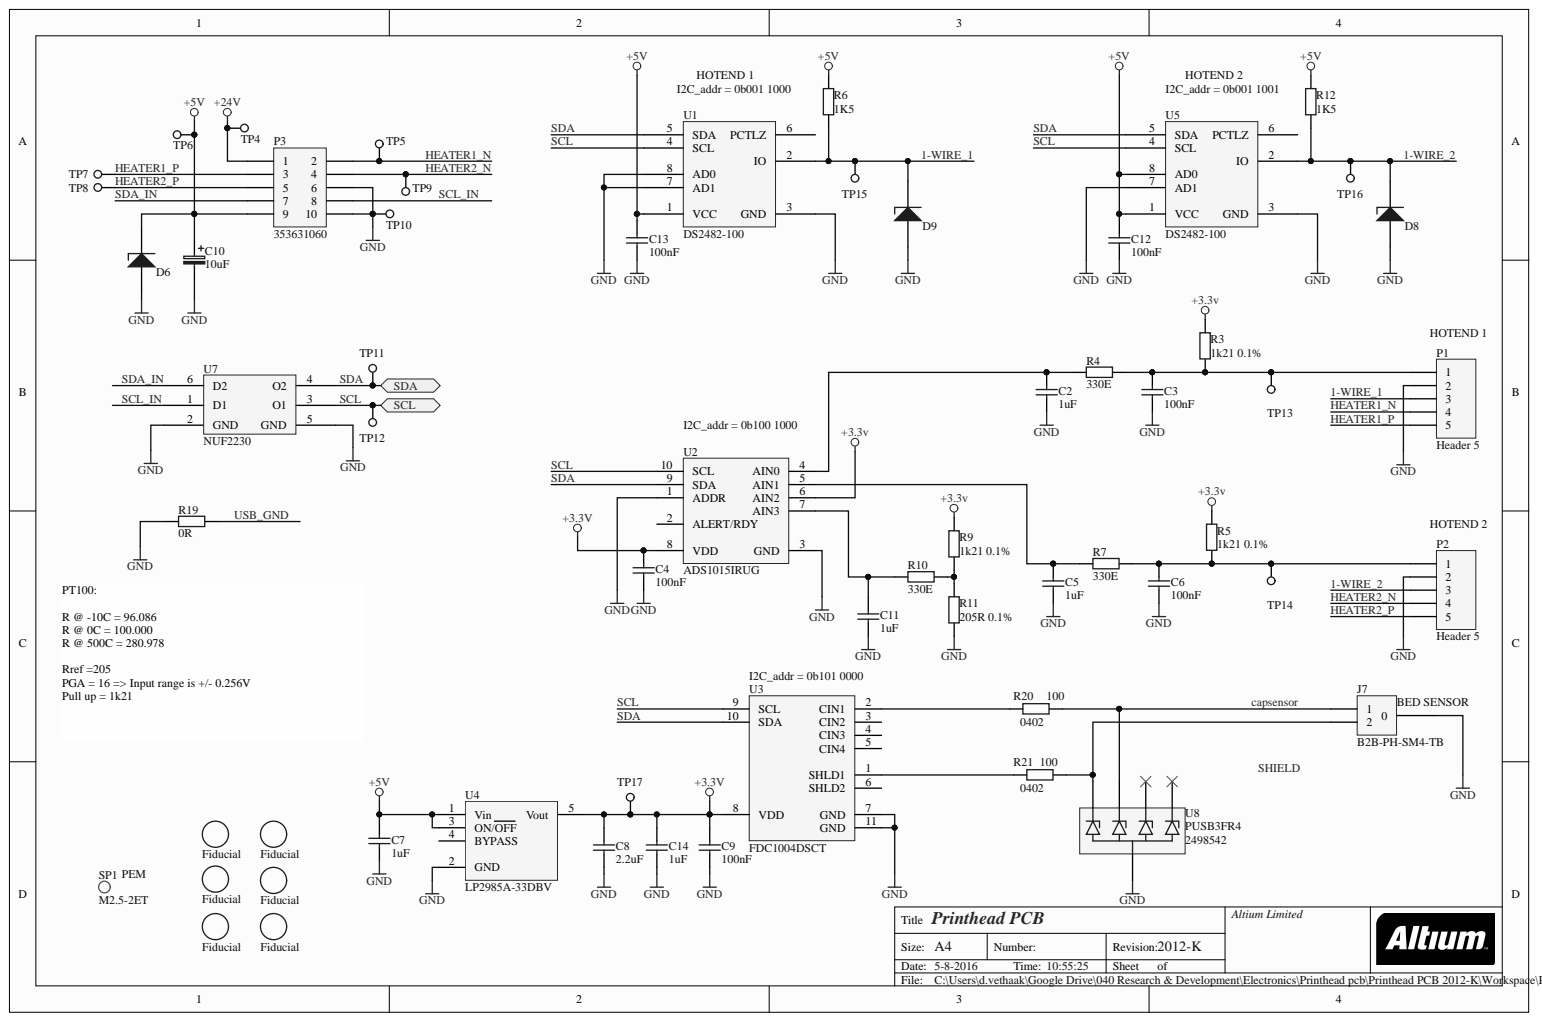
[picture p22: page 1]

Rref =205
PGA = 16 => Input range is +/- 0.256V
Pull up = 1k21

Title | Altium Limited Printhead PCB

Size: A4 | Number: | Revision: 2012-K
Date: 5-8-2016 Time: 10:55:25 | | Sheet of

C:\Users\d.vethaak\Google Drive\040 Research & Development\Electronics\Printhead pcb\Printhead PCB 2012-K\Workspace\Printhead.SchDoc

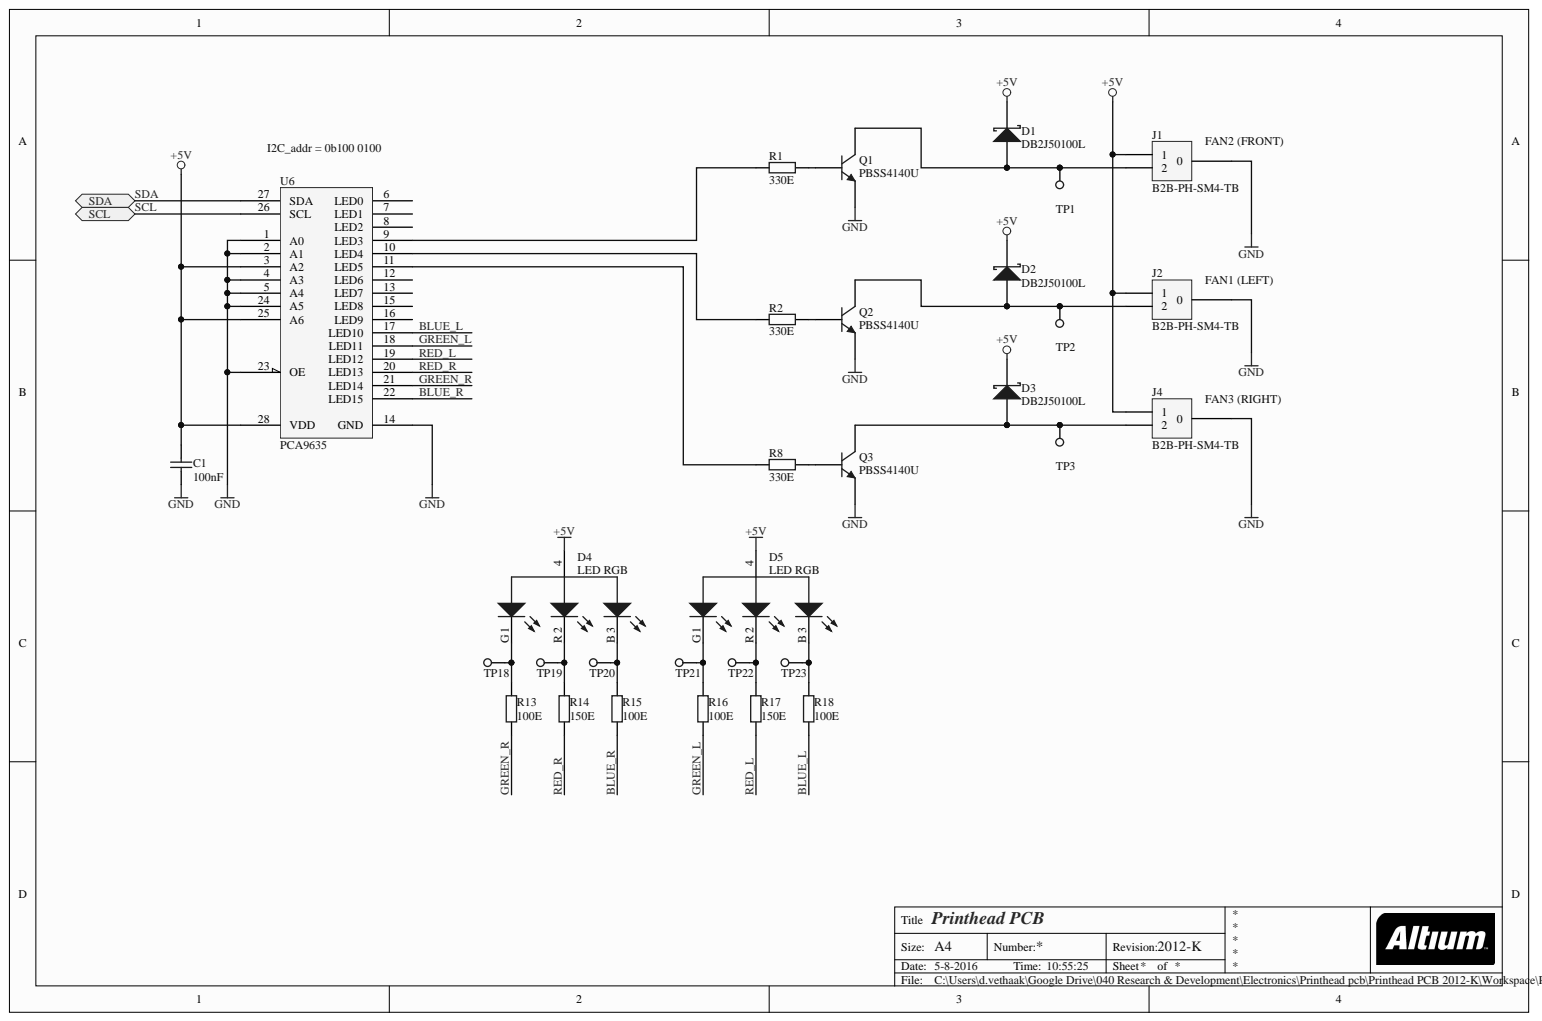
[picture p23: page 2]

Title | **** *

Size: A4 | Number: | Revision:

C:\Users\d.vethaak\Google Drive\040 Research & Development\Electronics\Printhead pcb\Printhead PCB 2012-K\Workspace\Printhead2.SchDoc

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
D | D
C | C
B | B
A | A
Printhead PCB Title | * * * * *
Size: A4 | Number: * | Revision: 2012-K
| | * *
C:\Users\d.vethaak\Google Drive\040 Research & Development\Electronics\Printhead pcb\Printhead PCB 2012-K\Workspace\Revisions.SchDoc

2012-K

## Changes in respect to 2012-J

DJV 26-07-2016 - changed ESD protection NUF2230 to PUSB3FR4, because of noise at cap sensor

## DJV 26-07-2016 - changed SHIELD plane on all layers DJV 26-07-2016 - added R20 and R21 between U3 and PUSB3FR4 DJV 26-07-2016 - added more GND vias on the edge of the GND planes

2012-J

## Changes in respect to 2012-I CDB 06-06-2016 - Removed copper under 0603 components

2012-I

## Changes in respect to 2012-H

CDB 27-05-2016 - Connected mechanical solder pins of J4, J7, J1 and J2 to GND for stronger

## connections

CDB 25-05-2016 - Changed U7 to NUF2230 CDB 25-05-2016 - Removed C17 CDB 25-05-2016 - Changed D8 and D9 to ESD9L5.0ST5G CDB 25-05-2016 - Added D6 CDB 25-05-2016 - Added R19 (this resistor will or will not be placed) CDB 25-05-2016 - Added ESD_GND polygon for better ESD properties CDB 25-05-2016 - Made via's near U3 and ESD_GND bigger to lower impedance

2012-H

## Changes in respect to V0.9 CdB 26-02-2016 - Removed D6 and D7 CdB 26-02-2016 - Added U7, U8, C14 and C17 CdB 26-02-2016 - Added back of SP1

V0.9

## Changes in respect to V0.8 CdB 08-11-2015 - Added TVS diodes D8 and D9 to 1-Wire lines

V0.8

## Changes in respect to V0.7.1 CdB 25-09-2015 - Changed board shape CdB 25-09-2015 - Switched sides of PT100 and Heater for both hot-ends CdB 25-09-2015 - Added text for top and bottom CdB 25-09-2015 - Added ground planes to top and bottom CdB 25-09-2015 - Added test points to fan outputs

V0.7.1

## Changes in respect to V0.7 CdB 25-08-2015 - Increased via size on U3

V0.7

## Changes in respect to V0.6 CdB 20-08-2015 - Changed fan and capacitive sensor connectors to SMD versions CdB 20-08-2015 - Re-did part of lay-out

V0.6

## Changes in respect to V0.5 CdB 20-08-2015 - Changed board shape CdB 20-08-2015 - Added SP1 CdB 20-08-2015 - Changed top connector to Molex 353631060 CdB 20-08-2015 - Completely re-did layout and routing CdB 20-08-2015 - Added test points

V0.5

Changes in respect to V0.25 CdB 29-06-2015 - Changed board shape CdB 29-06-2015 - Completely re-did layout and routing CdB 29-06-2015 - Added i2c to 1 wire masters CdB 29-06-2015 - Changed JST connectors to spring loaded connectors CdB 29-06-2015 - Changed led driver to one with more outputs CdB 29-06-2015 - Added RGB leds

V0.25

## Changes in respect to V0.2: CdB 27-01-2015 - Removed solder mask between pads in fine pitch components CdB 27-01-2015 - Removed silk screen between fine pitch components CdB 27-01-2015 - Added tin thieves to connector J3 CdB 27-01-2015 - Added revision sheet CdB 27-01-2015 - Added tooling holes

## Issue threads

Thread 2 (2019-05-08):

build firmware ultimaker.

samuelvincenzome, 2019-05-08:
Hi, My name is Samuel de Vincenzo and I built the printed circuit board as described in the PCBs File folder.
My question is how do I save the firmware on the card chip and what firmware can I use.

Thank you!

Samuel

736984325, 2019-05-08:
you can use malin firmware by Arduino IDE,and you could visit some 3d printer websites to find more information

---Original---
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

Ghostkeeper, 2019-05-09:
@CoenSchalkwijk Wasn't there an image that you could download somewhere?

There are two firmwares: One is Marlin that goes on the microcontroller board, and the other is a Linux installation that goes on the main PCB.

CoenSchalkwijk, 2019-05-13:
There's a .hex file in the image/swu file. This is the Marlin image for the main board of the printer, not the olimex board.

Ghostkeeper, 2019-05-13:
Is it possible to download the main Olimex Linux image?

CoenSchalkwijk, 2019-05-15:
Both are provided in a _single_ package. It's currently not possible to just browse through our firmware repository. You'll need to know the exact version numbers you're looking for. Which are provided by a 'version.txt' file, which only points to the latest-and-greatest. @samuelvincenzome are you looking for the PCB/atmel firmware (a hex file, containing our Marlin implenentation) or controlling system firmware (a debian based linux image)?

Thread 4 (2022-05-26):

Bug in latest ultimaker 3 firmware

acca84, 2022-05-26:
Hello
I think i have found a bug in latest UM3 firmware

If i start a print and cancel it from LCD menu, the print stops as excepted but the material is unloaded.
It occurs when printing with printhead number 2, i didn't try using printhead number 1

Do anyone has the same behaviour ?
Thanks

ckielstra, 2022-06-09:
@acca84 Thank you for reporting this bug. I'm not aware this bug has been reported before, so it is a situation that happens with few people. Ultimaker recommends you to do prints with printhead 1 when possible, the left printhead is firmly attached and will give the most accurate print results.

Since sales of the UM3 printer stopped a few years ago, only bugs will be fixed that make it impossible to use the printer. This bug is annoying and we'd love to see it fixed, but given the limited resources we have it's not going to be fixed.

Closed 2022-06-09.

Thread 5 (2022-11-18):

Redundant Cool Down Procedure on Abort

3Duke3, 2022-11-18:
If a print job is started by selecting a file from usb, then immediately aborted (usually due to accidentally selecting the wrong file), the machine cycles through a lengthy cool down procedure, regardless of the print cores temperature at time of abort. The machine is locked and unresponsive until the cool-down procedure is completed, or if the machine is power cycled.

The problem is if you start a print job, and immediately abort it before anything has had a chance to reach any meaningful temperature, the cool down procedure redundantly invokes the continued heating of print cores until they reach a defined temperature, and then actively cools them back down before allowing you to start a new print job.

What should happen: If the print job is aborted before any material is extruded (or perhaps before cores reach a certain temperature), then no cool down procedure should be necessary, and the user can select a new print job immediately.

3Duke3, 2022-11-22:
Have just noticed this doesn't happen every time. I need to investigate further but I suspect it may have some relation to weather or not the second extruder/hotend is required for the print job.

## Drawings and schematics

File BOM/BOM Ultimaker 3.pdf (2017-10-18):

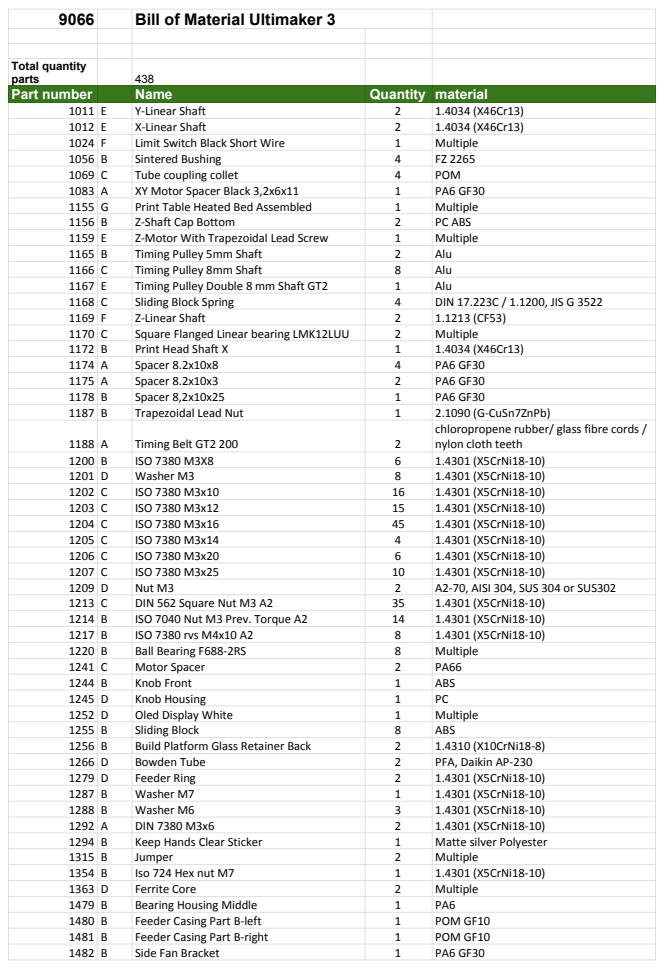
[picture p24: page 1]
Total quantity; parts; Part number; Name; Quantity material; Y-Linear Shaft; X-Linear Shaft; Limit Switch Black Short Wire; Multiple; Sintered Bushing; Tube coupling collet; POM; XY Motor Spacer Black 3,2x6x11; Print Table Heated Bed Assembled; Z-Shaft Cap Bottom; PC ABS; Z-Motor With Trapezoidal Lead Screw; Timing Pulley 5mm Shaft; Alu; Timing Pulley 8mm Shaft; Timing Pulley Double 8 mm Shaft GT2; Sliding Block Spring; DIN 17.223C / 1.1200, JIS G 3522; Z-Linear Shaft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

9066 Bill of Material Ultimaker 3

chloropropene rubber/ glass fibre cords /
nylon cloth teeth

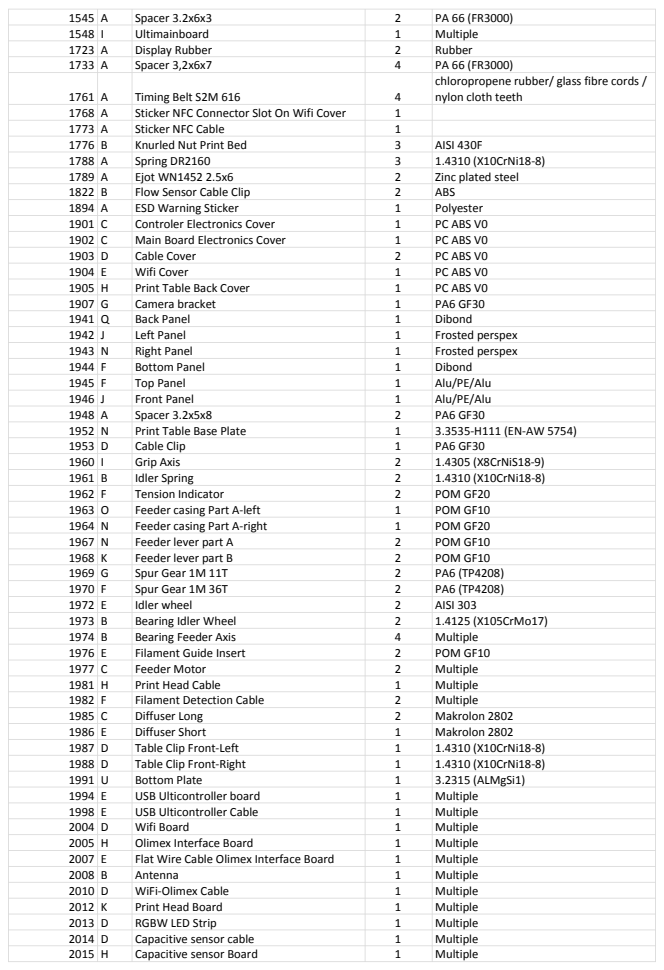
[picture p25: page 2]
Spacer 3.2x6x3; Ultimainboard; Multiple; Display Rubber; Rubber; Spacer 3,2x6x7; Timing Belt S2M 616; Sticker NFC Connector Slot On Wifi Cover; Sticker NFC Cable; Knurled Nut Print Bed; AISI 430F; Spring DR2160; 1.4310 (X10CrNi18-8); Ejot WN1452 2.5x6; Zinc plated steel; Flow Sensor Cable Clip; ABS; ESD Warning Sticker; Polyester; Controler Electronics Cover; PC ABS V0; Main Board Electronics Cover; Cable Cover; Wifi Cover; Print Table Back Cover; Camera bracket; Back Panel; Dibond; Left Panel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

chloropropene rubber/ glass fibre cords /
nylon cloth teeth

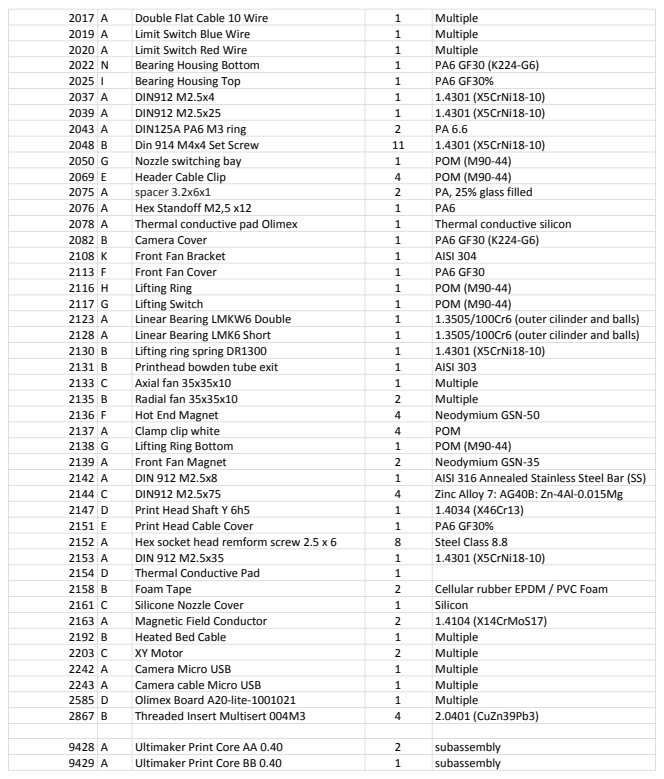
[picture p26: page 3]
Double Flat Cable 10 Wire; Multiple; Limit Switch Blue Wire; Limit Switch Red Wire; Bearing Housing Bottom; Bearing Housing Top; DIN912 M2.5x4; 1.4301 (X5CrNi18-10); DIN912 M2.5x25; DIN125A PA6 M3 ring; Din 914 M4x4 Set Screw; Nozzle switching bay; POM (M90-44); Header Cable Clip; spacer 3.2x6x1; PA, 25% glass filled; Hex Standoff M2,5 x12; Thermal conductive pad Olimex; Thermal conductive silicon; Camera Cover; Front Fan Bracket; AISI 304; Front Fan Cover; Lifting Ring; Lifting Switch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

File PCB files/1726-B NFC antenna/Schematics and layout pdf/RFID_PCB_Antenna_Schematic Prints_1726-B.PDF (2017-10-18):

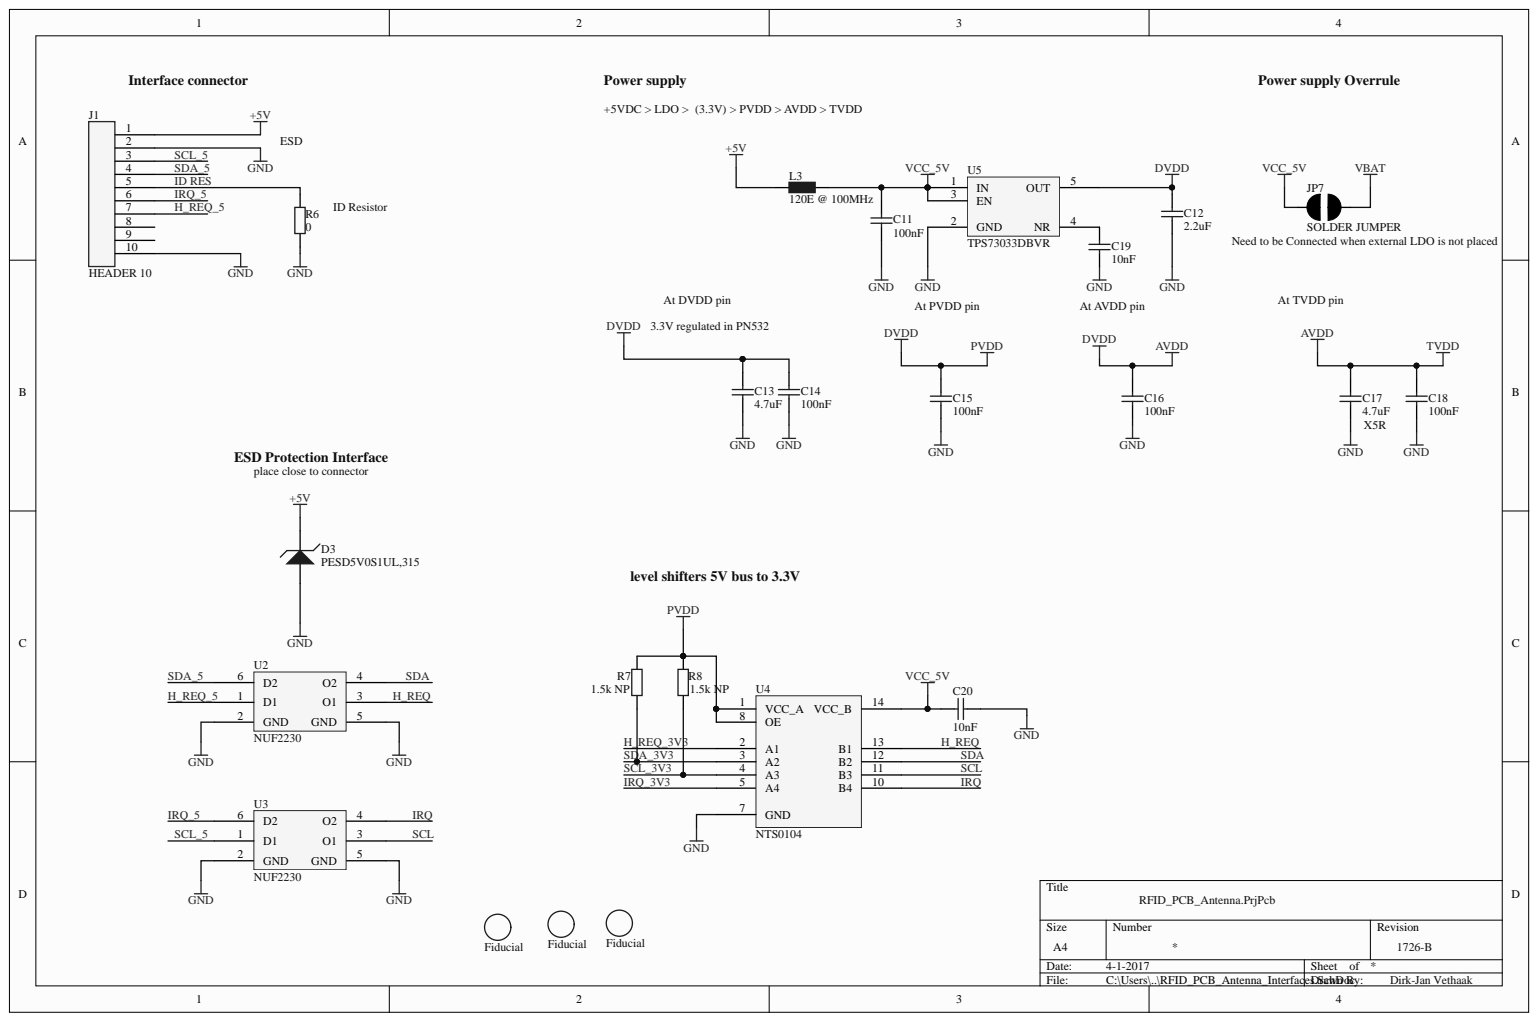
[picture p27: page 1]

+5VDC > LDO > (3.3V) > PVDD > AVDD > TVDD

Need to be Connected when external LDO is not placed

ESD Protection Interface
place close to connector

level shifters 5V bus to 3.3V

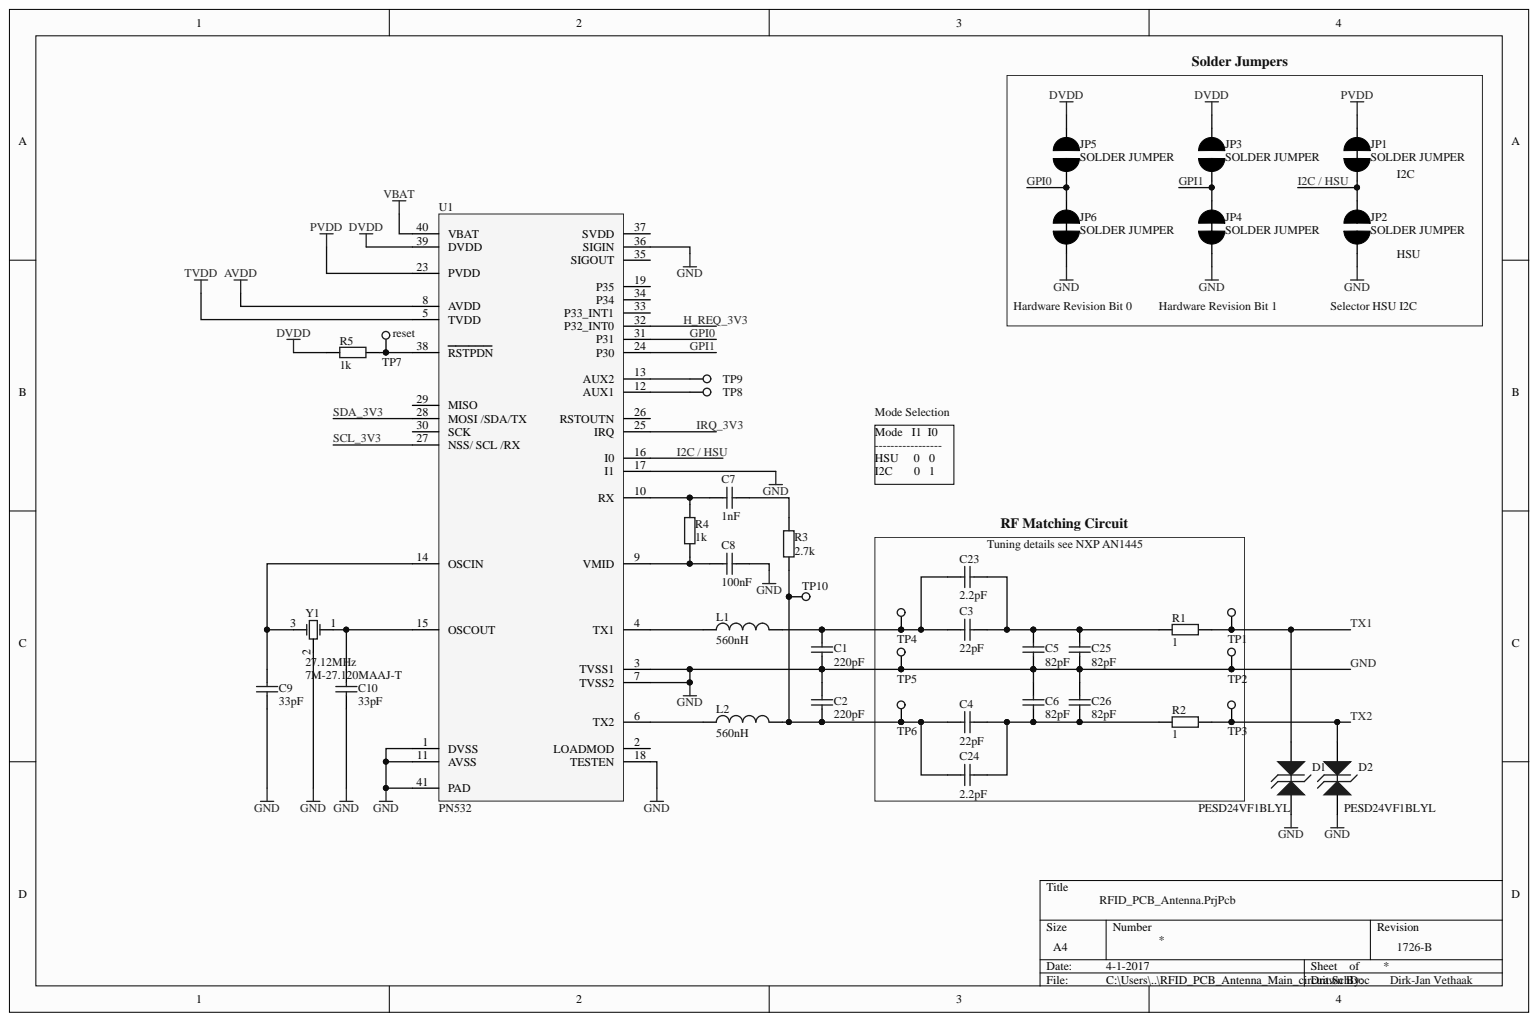
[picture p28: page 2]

C23 | | Tuning details see NXP AN1445

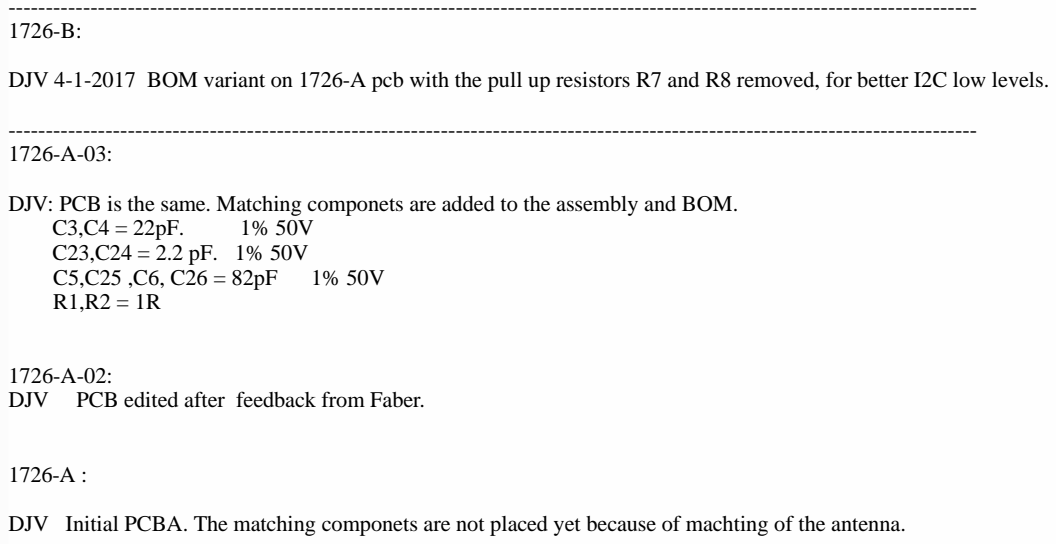
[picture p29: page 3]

DJV 4-1-2017 BOM variant on 1726-A pcb with the pull up resistors R7 and R8 removed, for better I2C low levels.

DJV: PCB is the same. Matching componets are added to the assembly and BOM.

DJV Initial PCBA. The matching componets are not placed yet because of machting of the antenna.

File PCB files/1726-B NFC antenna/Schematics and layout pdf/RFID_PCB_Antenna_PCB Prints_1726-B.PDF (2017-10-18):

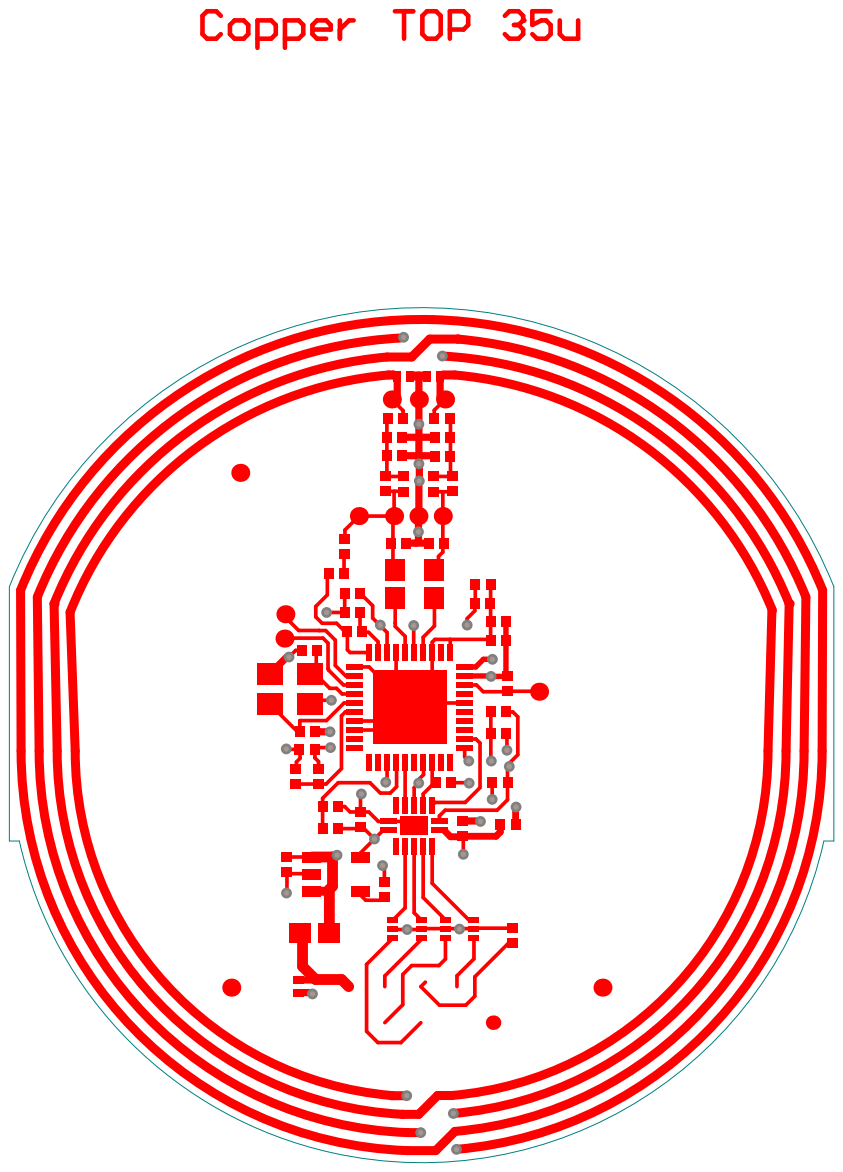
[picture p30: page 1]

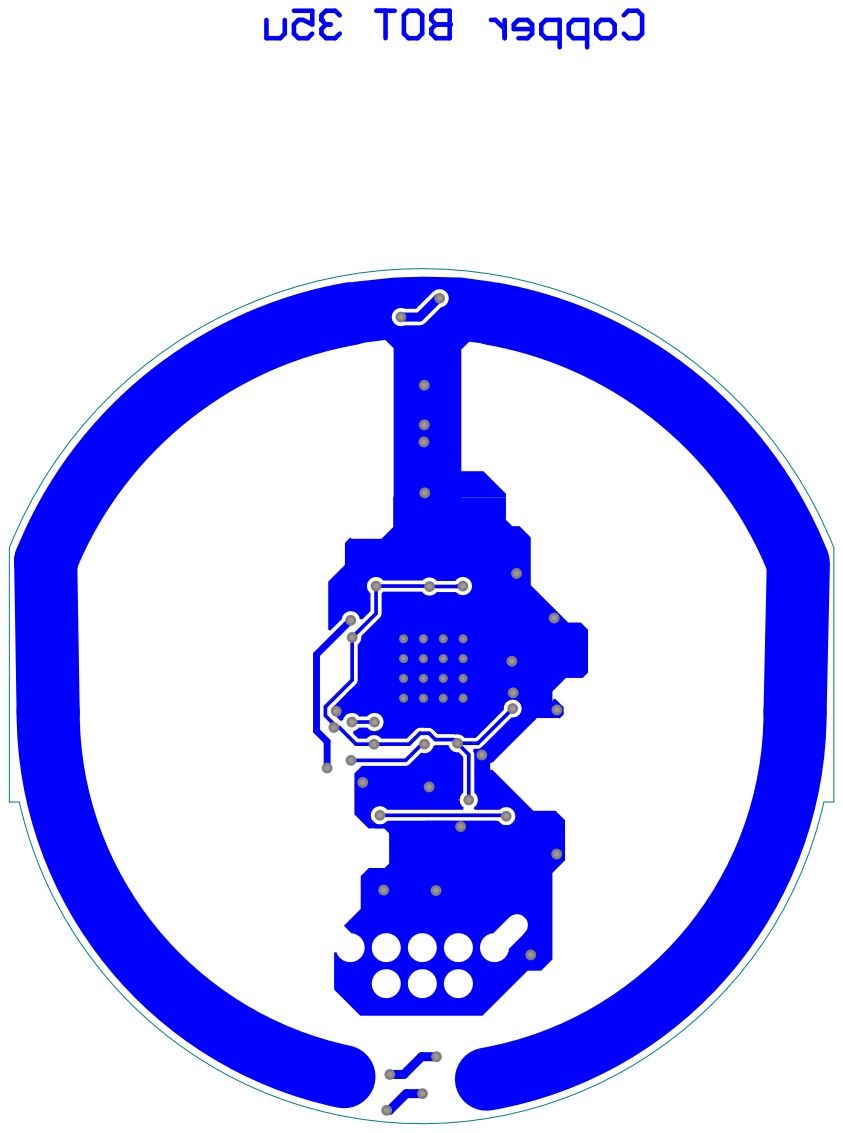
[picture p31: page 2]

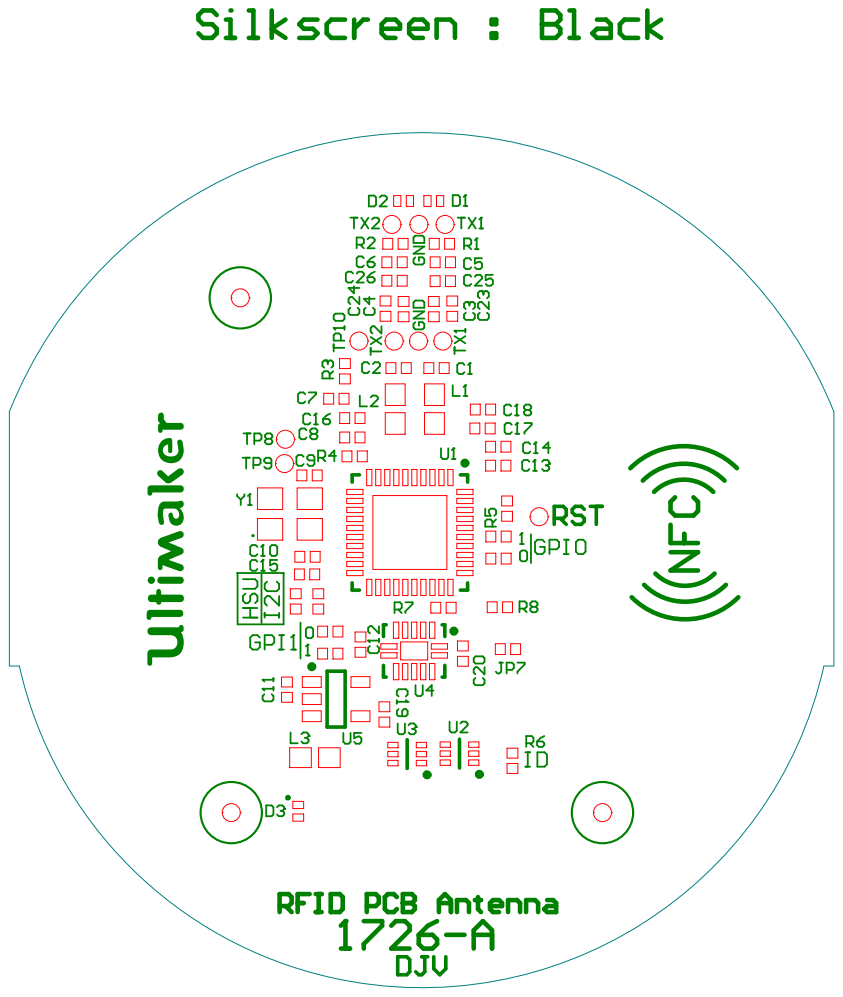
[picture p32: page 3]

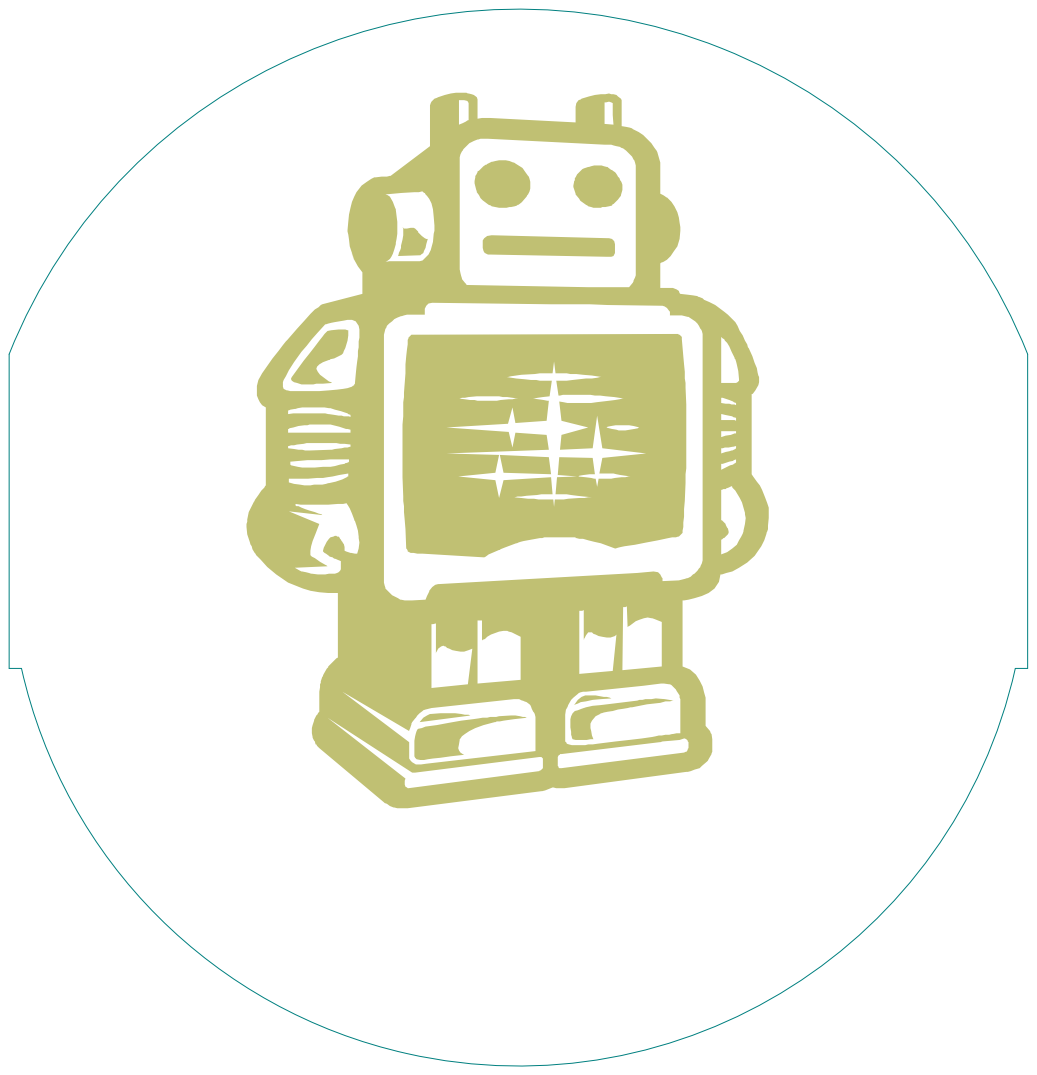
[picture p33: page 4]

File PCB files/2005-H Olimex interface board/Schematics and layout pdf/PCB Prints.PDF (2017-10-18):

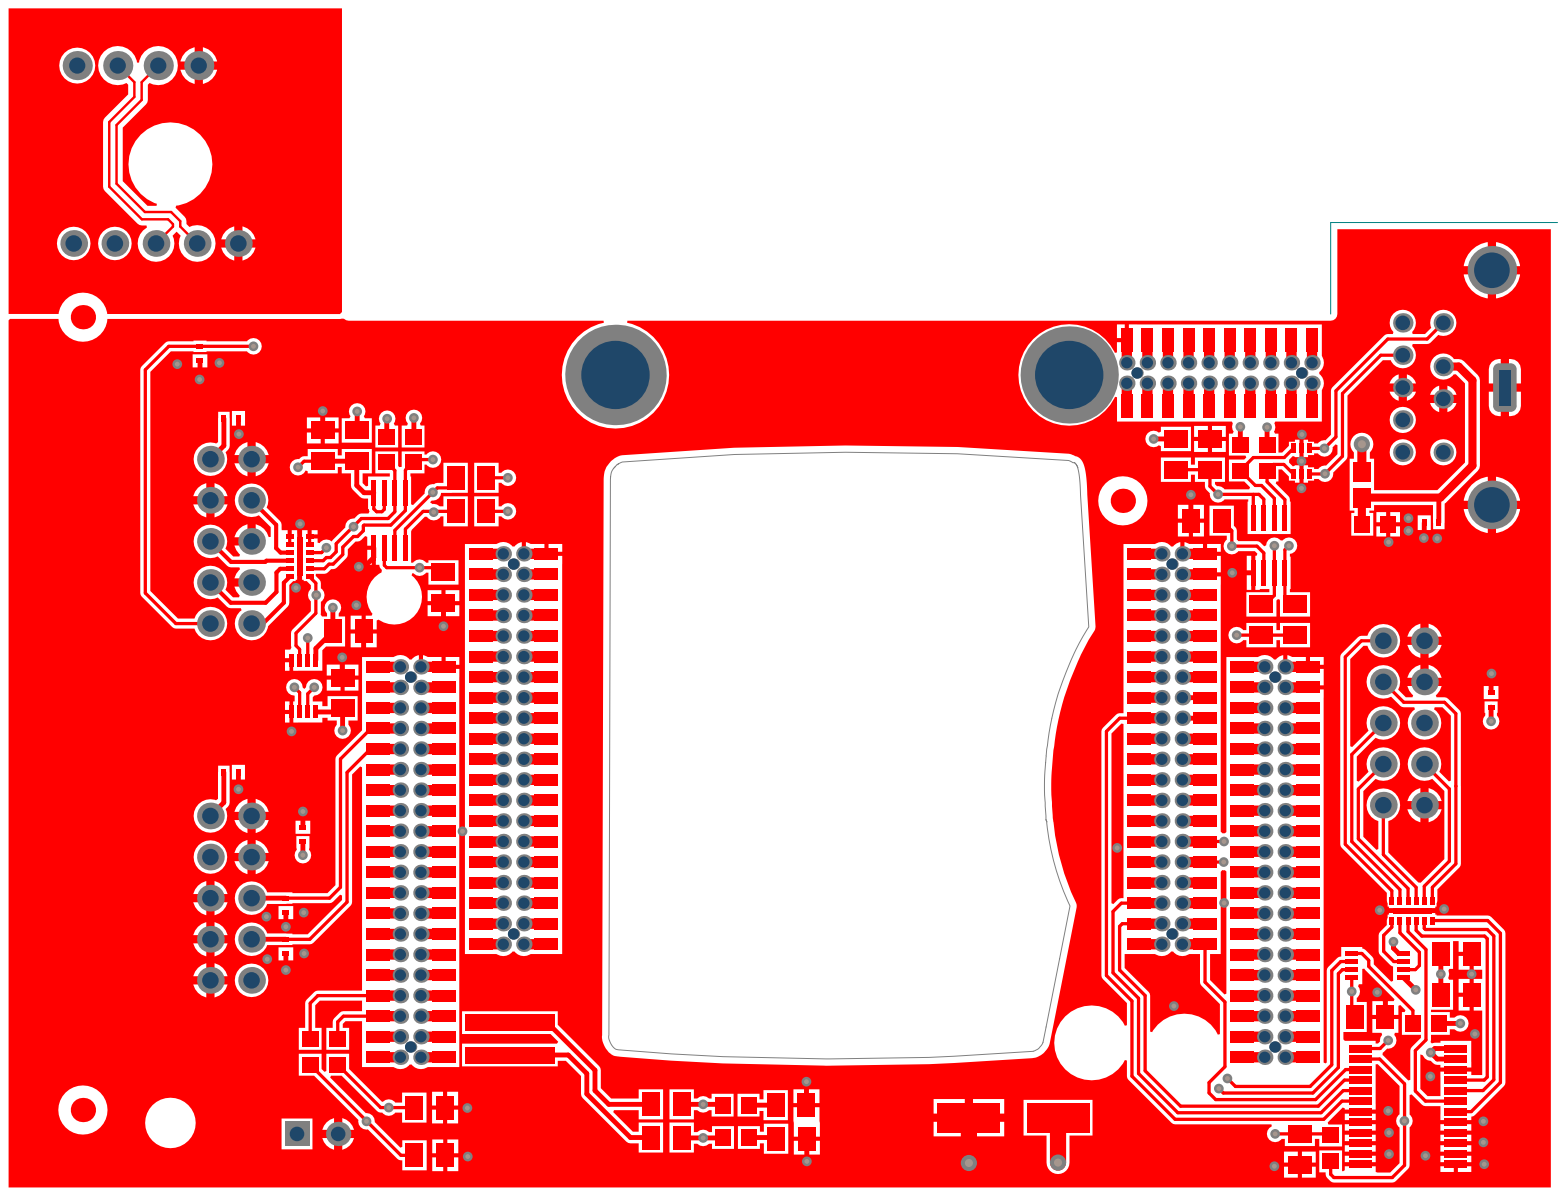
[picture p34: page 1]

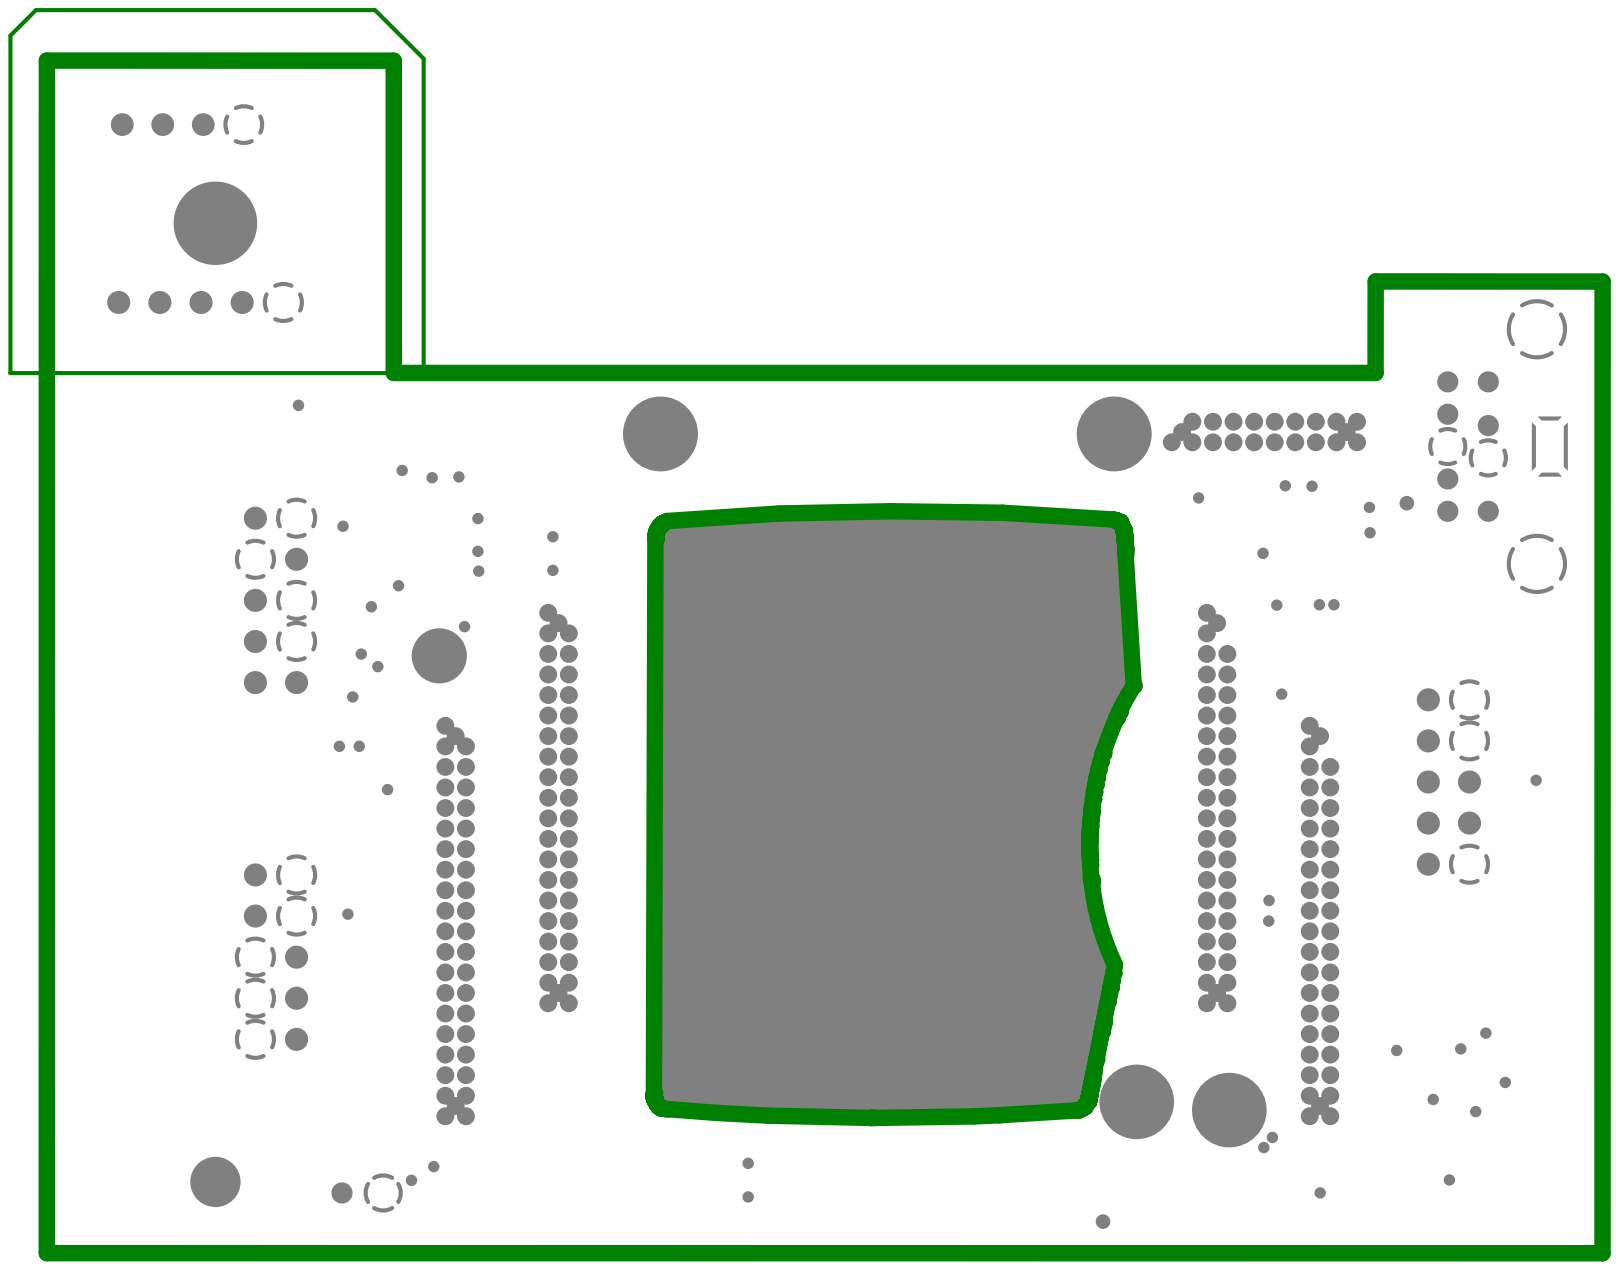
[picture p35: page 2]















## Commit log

2017-10-18 initial commit
    ultimaker 3 files
    [1011-E.STEP, 1012-E.STEP, 1024-F.STEP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]
2017-10-19 Updated the wrong untested development version to the currently shipped version
    We continuously improve our product and by accident a version was
    uploaded with a silicone flap and a front fan bracket that are still in
    experimental phase. The idea of these files is to reflect the state of
    the currently shipped machines.
2017-10-23 added missing reel holder assembly
    added missing reel holder assembly
    [1725-G.STEP, 1726-B.STEP, 1727-C.STEP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]
